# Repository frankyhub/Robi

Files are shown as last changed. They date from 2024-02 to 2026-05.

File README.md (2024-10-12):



<div align="center">

|[:skull:ISSUE](https://github.com/frankyhub/Robi/issues?q=is%3Aissue)|[:speech_balloon: Forum /Discussion](https://github.com/frankyhub/Robi/discussions)|[:grey_question:WiKi](https://github.com/frankyhub/Robi/wiki)||
|--|--|--|--|
| | | | |
||<a href="https://github.com/frankyhub/Robi/issues">|<a href="https://github.com/frankyhub/Robi/discussions">|<a href="https://github.com/frankyhub/Robi/releases">|
|| <a href="https://github.com/frankyhub/Robi/pulse" alt="Activity">| <a href="https://github.com/frankyhub/Robi/graphs/traffic">  |<a href="https://github.com/frankyhub?tab=stars"> |
</div>

# Robi
 ## 3D-Druck- und Lasercutter-Version

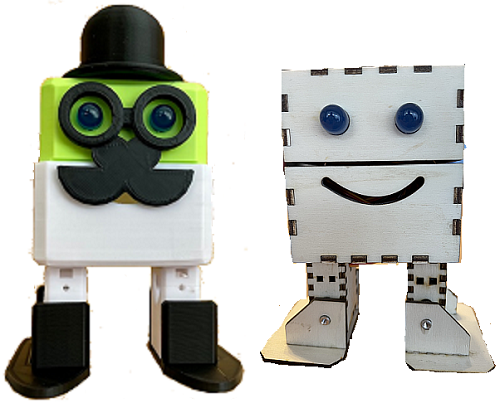
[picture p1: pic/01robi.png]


## Robi Lasercutter Montage Anleitung

## Story:
Diese Anleitung beschreibt die Montage eines Roboters. Robi kann laufen, tanzen und den Moonwalk. Jedes Bein hat zwei Gelenke, die von Servo-Motoren bewegt werden. Als Steuerung dient ein Arduino NANO, gespeist von einer 9V-Batterie.
Die Robi-Elemente werden aus einer 3mm Sperrholzplatte gelasert, ebenso ist ein 3D-Druck Gehäuse möglich.

## Entwerfe dein eigenes Robi Design mit Inkscape

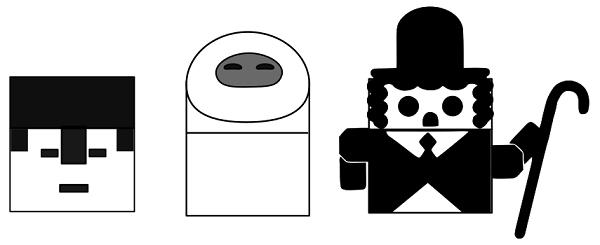
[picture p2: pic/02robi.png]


Downlaod [Inkscape-Vorlage](svg/Charley.svg)

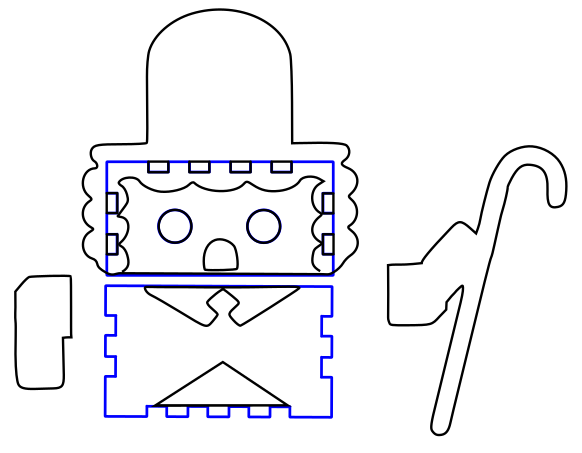
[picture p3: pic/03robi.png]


## Die Stückliste:

| Anzahl | Bezeichnung | 
| --- | --- |
| 1  | Sperrholzplatte 300x300x3mm  | 
|  1 | NANO-Shield  | 
| 1  | Arduino NANO V3  | 
|  1 | NANO-Shield  | 
| 1  |  40 Pin Male 2,54mm Stiftleisten einreihig für das NANO-Shield | 
|  1 |  40 Pin Female 2,54 mm Buchsenleiste einreihig für das NANO-Shield | 
| 1  | Schalter 1 polig  | 
| 2  | Jumbo LEDs  | 
| 1  | 1K Ohm Widerstand  | 
| 1  | 9V Batterie  | 
| 1  | 9V Batterie-Klipp  | 
| 4  | Servo Motore SG90  | 
| 2  | Zylinderkopf Schrauben M3x8  | 
| 1  | Kabelbinder 10cm  | 
| 1  | Holzleim  | 
| 1  | Sekundenkleber  | 
| 1  | 20cm Schaltlitze 0,25mm2  | 

## Bauteilbilder der Stückliste

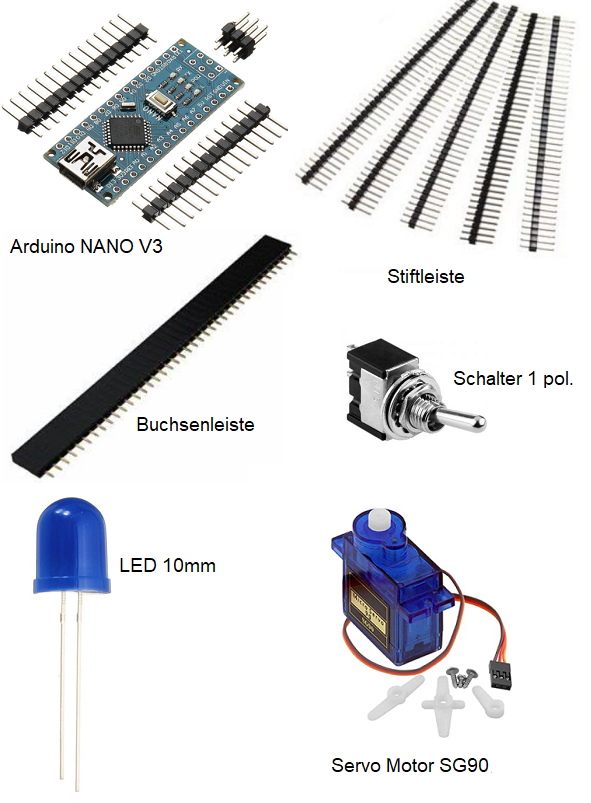
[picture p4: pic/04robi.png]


## Der NANO mit [Shield](https://github.com/frankyhub/KiCad-Shield/tree/main/NANO_Bot) und Stiftleisten

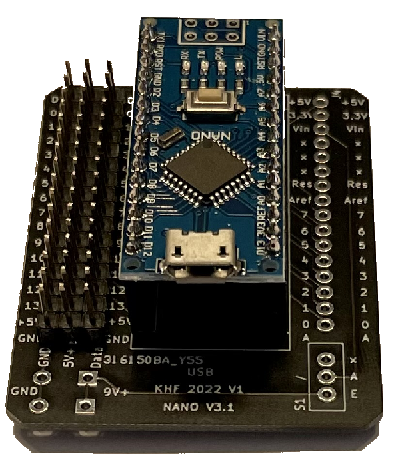
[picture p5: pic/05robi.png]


## Aufbau und Montage

Der Aufbau und die Montage von Robi ist in mehrere Schritte unterteilt

## Schritt 1: 
Überprüfe die Laserteile auf Vollständigkeit.
Verwende die Lasercutter Vorlage, bestehend aus:
+ 1 x Kopf Oberteilteil
+ 1 x Kopf Unterteil
+ 2 x Füße
+ 2 x Schuhe

Lasercutter-Datei (3mm Sperrholz)

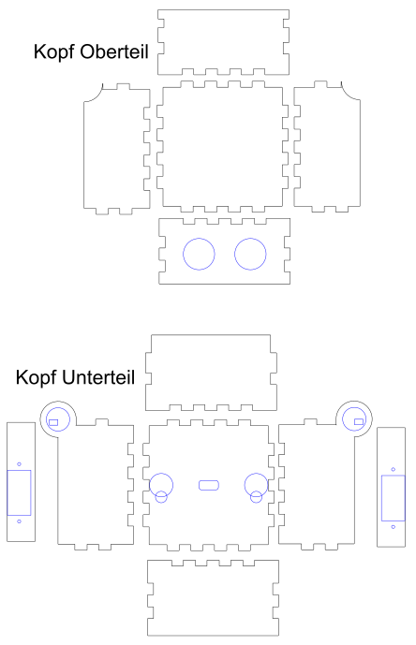
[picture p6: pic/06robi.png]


 Füße und Schuhe (3mm Sperrholz)

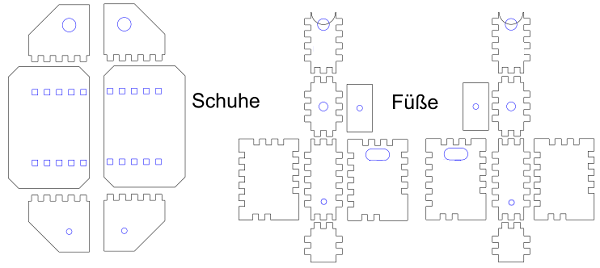
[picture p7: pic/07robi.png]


## Schritt 2: 
Das Kopf Oberteil montieren.

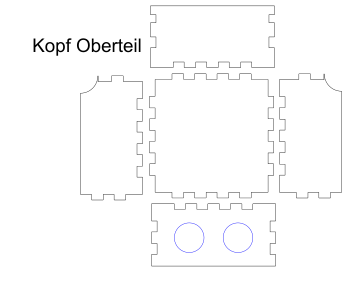
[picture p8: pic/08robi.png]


## Schritt 3: 
Das Kopf Unterteil montieren.
Achtung: Das rechte und linke Seitenteil mit dem Gelenk zum Schluss zusammen mit dem Kopf Oberteil montieren!

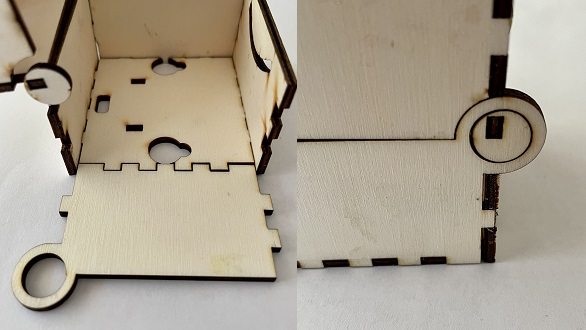
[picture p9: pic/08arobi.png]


Im Kopf Unterteil die Halterungen für die Servos kleben

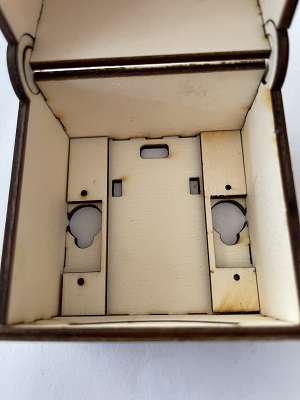
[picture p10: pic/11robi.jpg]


Die Hülle der beiden Füße verkleben.
Achtung: Wir benötigen zwei Füße. Die Öffnungen für die Servokabel sind jeweils innen und die Servos zeigen nach vorne!

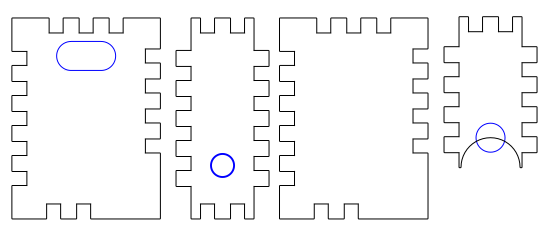
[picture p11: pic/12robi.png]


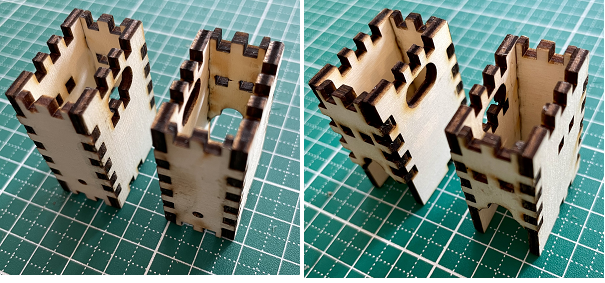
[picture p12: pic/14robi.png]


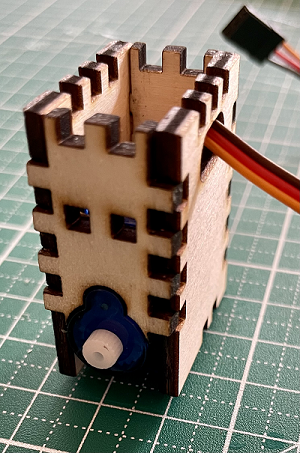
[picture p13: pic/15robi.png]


Die beiden Oberteile der Füße deckungsgleich verkleben (noch nicht an die Füße kleben!).

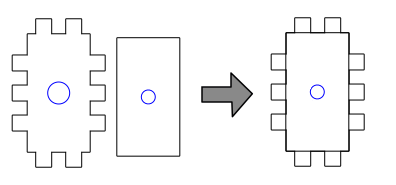
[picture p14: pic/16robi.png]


Die Oberteile der Füße werden an den Servo im Kopfteil geschraubt.

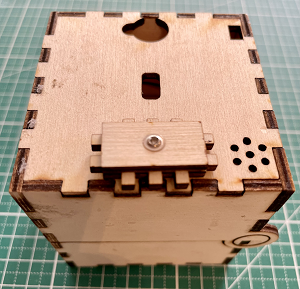
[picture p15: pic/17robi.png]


Alternativ können zu besseren Stabilität auch die 3D-Druck Teile verwendet werden.

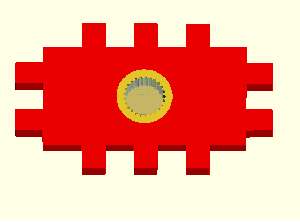
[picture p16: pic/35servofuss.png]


## Schritt 4: 
Den Robi verdrahten, die Bauteile jedoch noch nicht in das Gehäuse montieren.

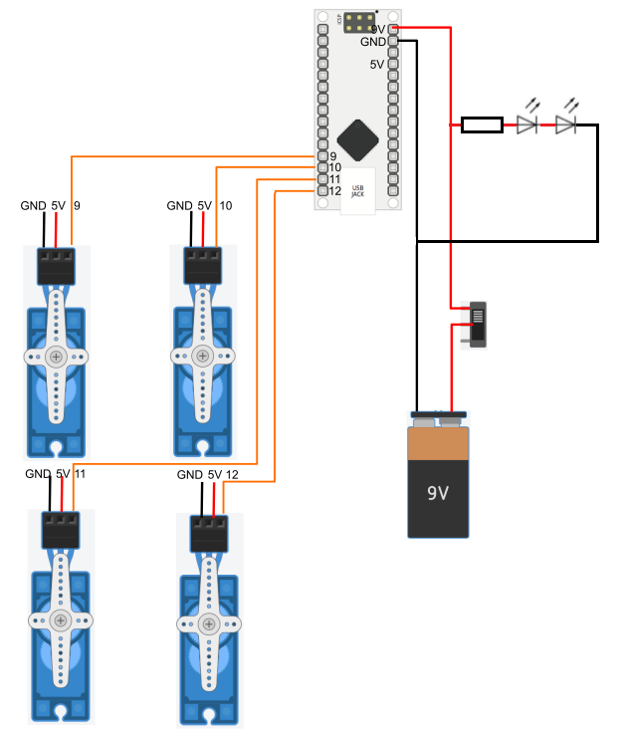
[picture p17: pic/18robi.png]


## Schritt 5: 
Vor der Montage der Servos ist ein Funktionstest sinnvoll:
Den Robi mit der Arduino IDE in C++ oder in Blocksprache programmieren.
Ist der Robi programmiert und sind die Servos in 90° Stellung, können sie in das Kopf-Unterteil und in die Füße montiert werden.

## Schritt 6: 
Die beiden Servos in 90° Stellung mit den unteren Kopfteil und den Oberteil der Füße verschrauben. Die Servos sollten durch die Verschraubung fest am Kopfteil sitzen. Anschließend die 9V-Batterie mit den Kabelbinder befestigen.

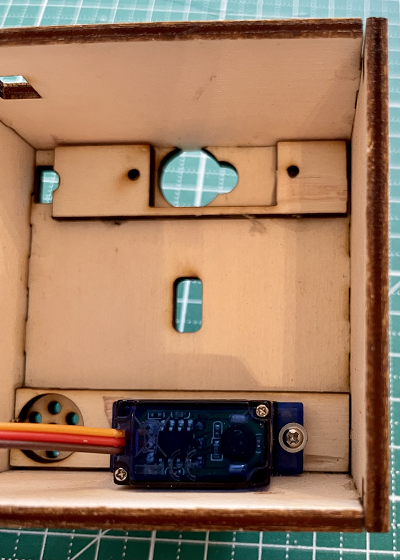
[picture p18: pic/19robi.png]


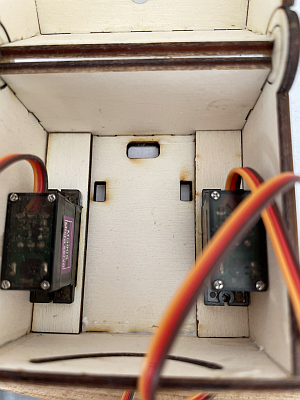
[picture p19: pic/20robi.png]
 

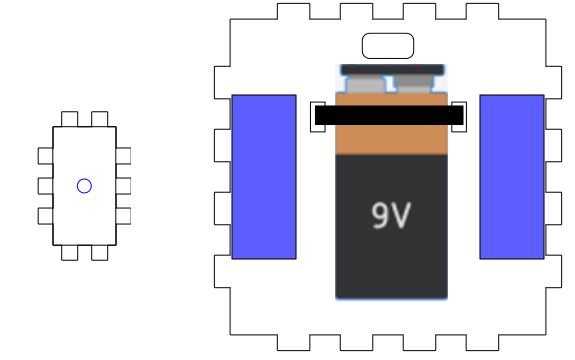
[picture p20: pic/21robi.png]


Die Schrittmotore in die Fußhülle montieren und das Fuß Unterteil ankleben

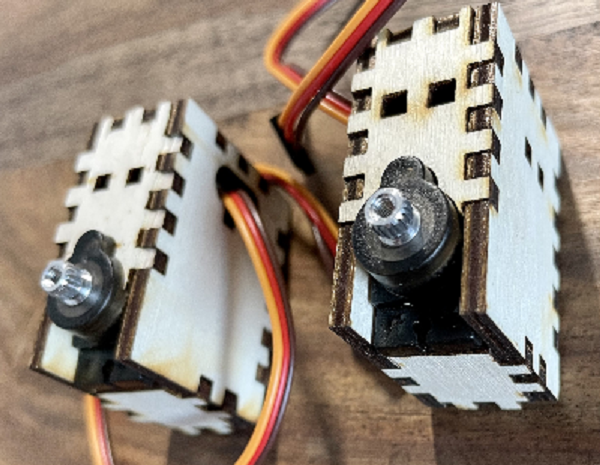
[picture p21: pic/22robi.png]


Die Schuhe an die Füße montieren

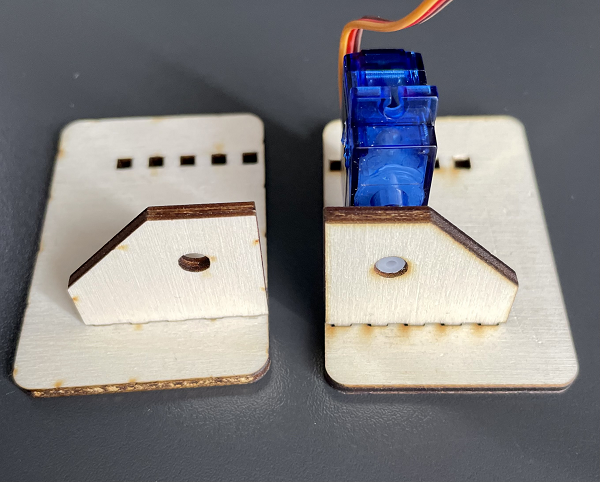
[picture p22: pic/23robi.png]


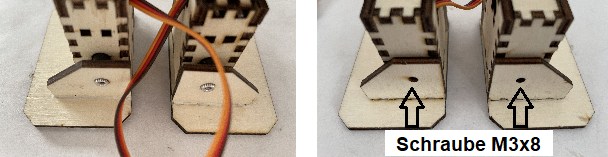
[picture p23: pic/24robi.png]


Die Servo-Kabel in den Body führen und die Füße an die Fußoberteile kleben

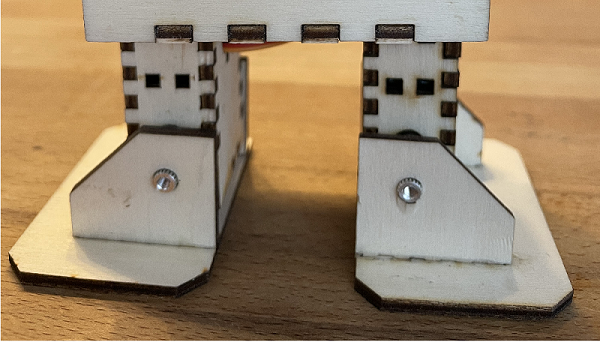
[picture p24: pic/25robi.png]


Alternativ können zu besseren Stabilität auch die 3D-Druck Teile verwendet werden.

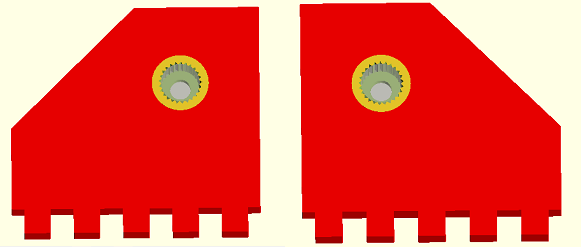
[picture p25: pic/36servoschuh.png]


## Schritt 7: 
Den NANO in das obere Kopfteil montieren
Platinenhalter auf das Shield kleben und das Shield anschließend in das innere, obere Kopfteil kleben. Daneben den Schalter montieren und verdrahten.
Vor dem endgültigen verkleben des NANOs in das Obere Kopfteil, sollte er fertig programmiert sein.
Optional noch zwei LEDs mit 1kOhm Vorwiderstand an 9V als Augen verwenden.

Einbau des NANO und der Battierie in den Robi-Kopfteil

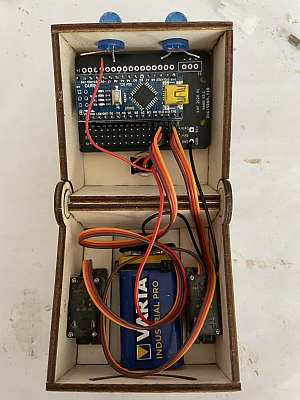
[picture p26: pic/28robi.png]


Anschlüsse der LEDs

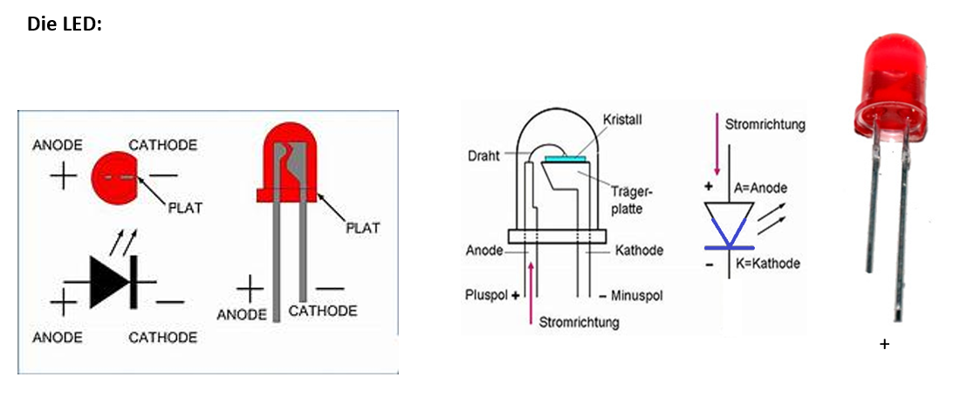
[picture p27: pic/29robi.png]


Anschluss des Batterieclips, des Schalters und der LEDs

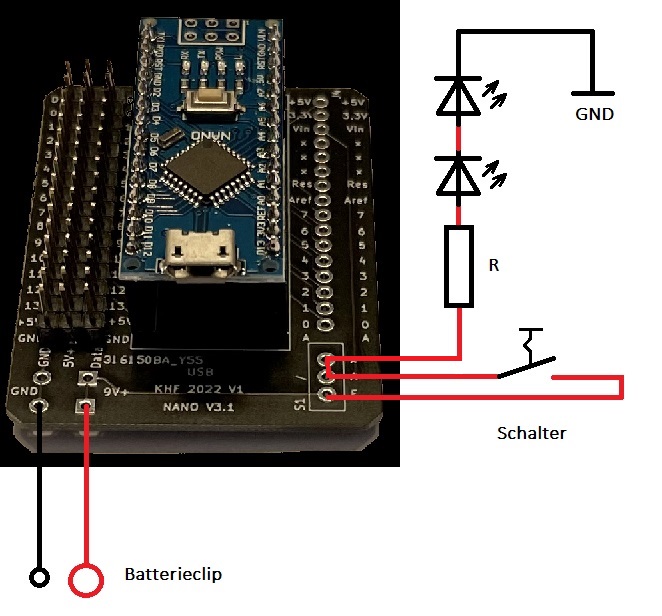
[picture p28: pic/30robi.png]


Fertig, Glückwunsch!

## Technische Hinweise

Anschlüsse des Servo-Motor SG90/MG90:

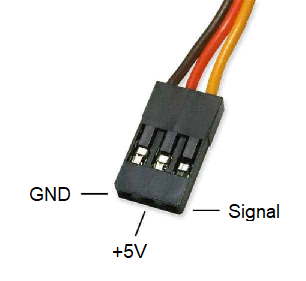
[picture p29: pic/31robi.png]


## Servo-Motor Impulsdiagramme:

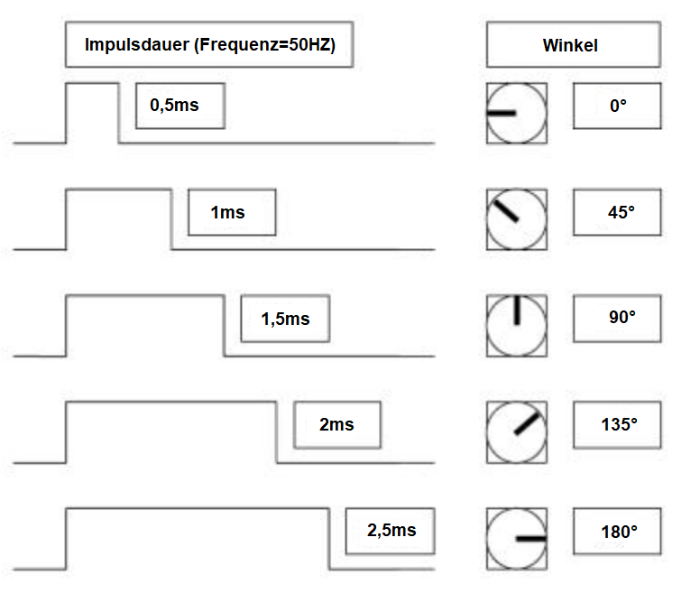
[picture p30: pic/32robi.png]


Impulsdiagramm: Ansteuerung des Servos mit einer Frequenz von 50 Hz:

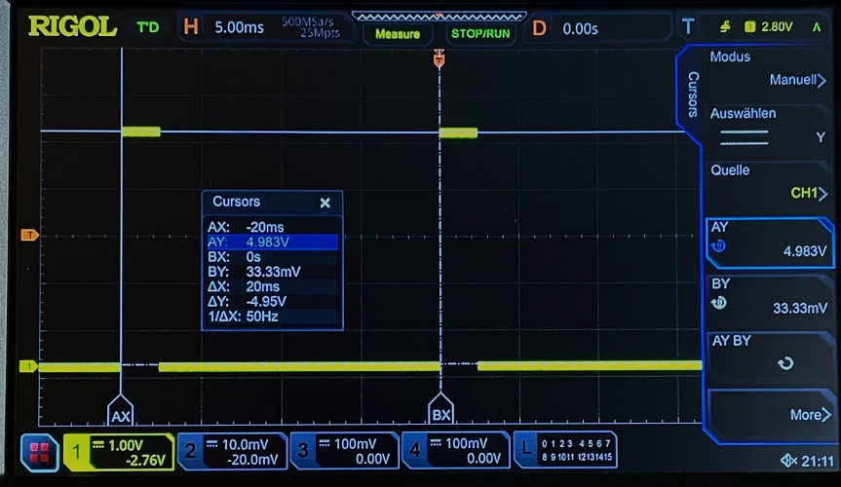
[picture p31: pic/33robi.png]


Impulsdiagramm: Ansteuerung des Servos mit einer Impulsbreite von 2,5ms (180°):

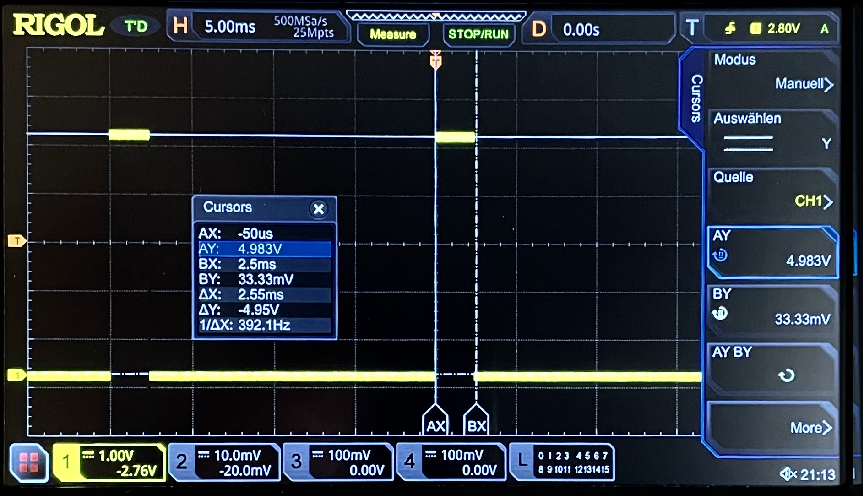
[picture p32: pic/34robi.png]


Blocky Beispiel Programme:

[Robi kalibirieren](blocky/robi_kalibrieren.bloc)

[Robi geht vorwärts](blocky/robi_vorwaerts.bloc)

[Robi tanzt I](blocky/robi_tanzt.bloc)

[Robi tanzt II](blocky/robi_zufall.bloc)

## Fertig!

---

<div style="position:absolute; left:2cm; ">   
<ol class="breadcrumb" style="border-top: 2px solid black;border-bottom:2px solid black; height: 45px; width: 900px;"> <p align="center"><a href="#oben">nach oben</a></p></ol>
</div>  

---

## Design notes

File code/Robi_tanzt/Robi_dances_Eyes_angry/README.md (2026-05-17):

## Robi angry eyes

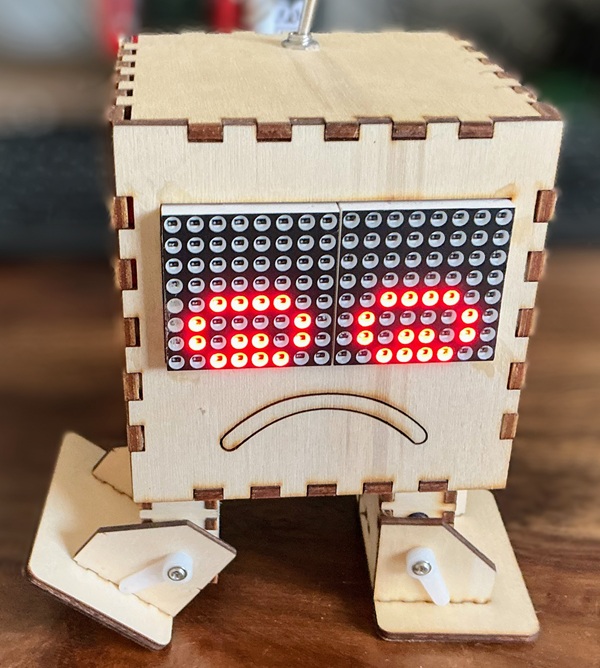
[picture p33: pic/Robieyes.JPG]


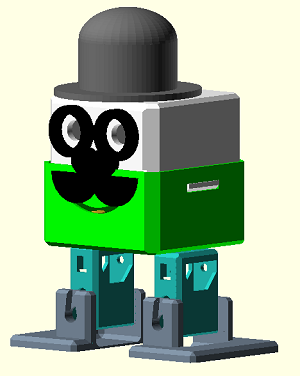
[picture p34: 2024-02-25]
pic/00robi.png

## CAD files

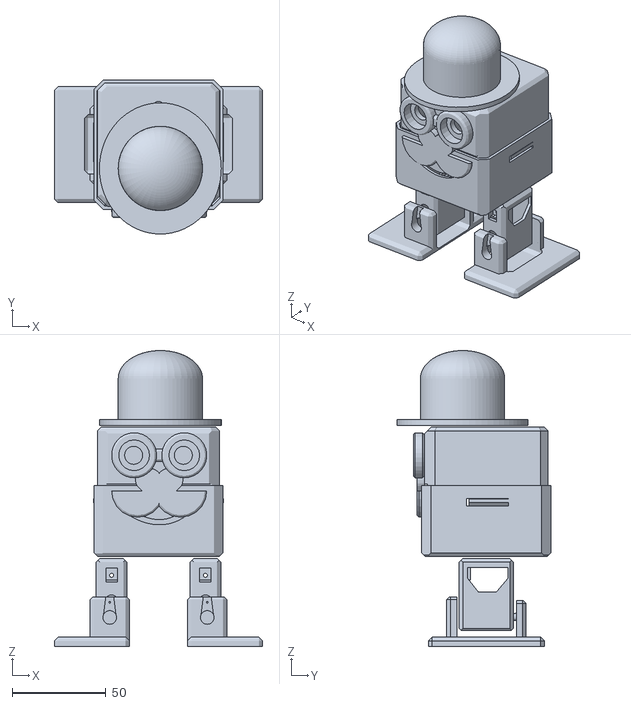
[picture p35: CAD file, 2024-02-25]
3D/Robi.stl
111.0 x 82.2 x 157.9

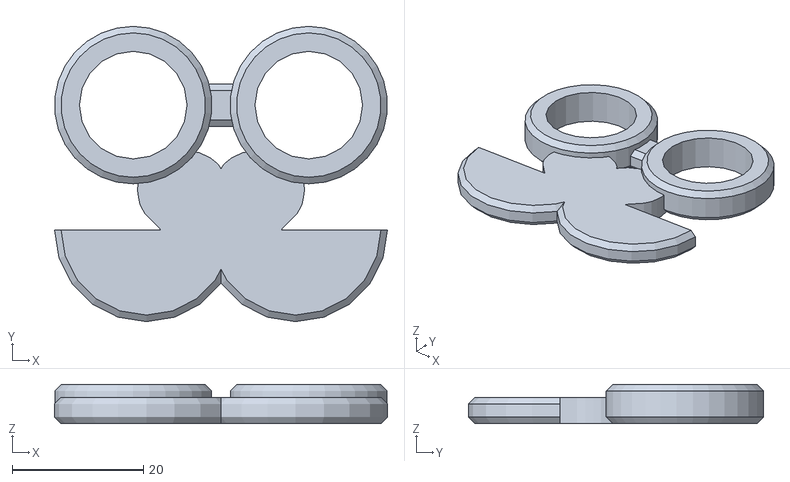
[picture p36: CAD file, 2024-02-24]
3D/Robi_Brille.stl
50.7 x 45.0 x 6.00

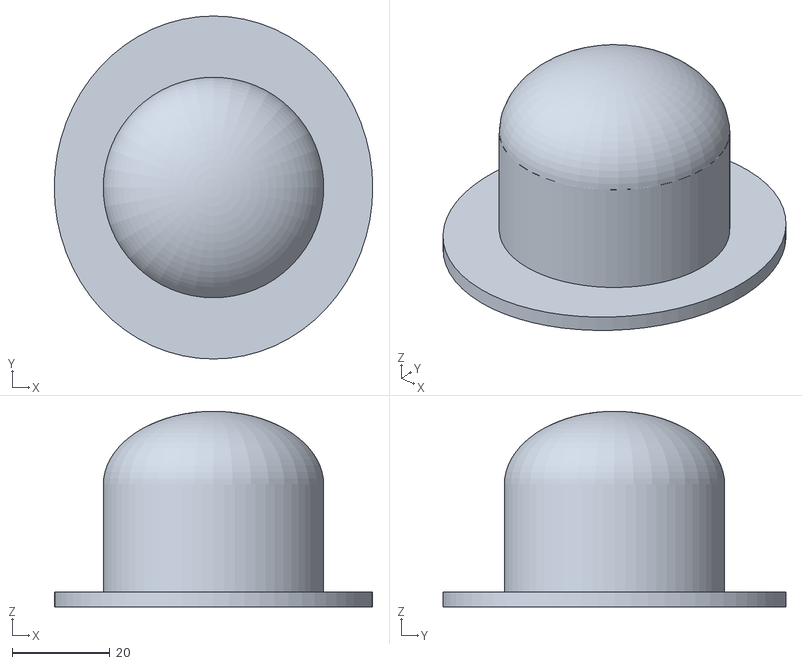
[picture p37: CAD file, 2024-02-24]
3D/Robi_Hut.stl
65.0 x 70.0 x 39.9

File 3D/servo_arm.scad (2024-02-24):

//Par. Servo Arm

arm_length = 7;

arm_count = 3; // [1,2,3,4,5,6,7,8]

//  Clear between arm head and servo head (PLA: 0.3, ABS 0.2)
SERVO_HEAD_CLEAR = 0.3; // [0.2,0.3,0.4,0.5]

$fn = 100 / 1;

/**
 *  Head / Tooth parameters
 *  Futaba 3F Standard Spline
 *  http://www.servocity.com/html/futaba_servo_splines.html
 *
 *  First array (head related) :
 *  0. Head external diameter
 *  1. Head heigth
 *  2. Head thickness
 *  3. Head screw diameter
 *
 *  Second array (tooth related) :
 *  0. Tooth count
 *  1. Tooth height
 *  2. Tooth length
 *  3. Tooth width
 */
FUTABA_3F_SPLINE = [
    [4.5, 5, 1.1, 2.5],
    [25, 0.4, 0.6, 0.0]
];

module servo_futaba_3f(length, count) {
    servo_arm(FUTABA_3F_SPLINE, [length, count]);
}

/**
 *  If you want to support a new servo, juste add a new spline definition array
 *  and a module named like servo_XXX_YYY where XXX is servo brand and YYY is the
 *  connection type (3f) or the servo type (s3003)
 */

module servo_standard(length, count) {
    servo_futaba_3f(length, count);
}

/**
 *  Tooth
 *
 *    |<-w->|
 *    |_____|___
 *    /     \  ^h
 *  _/       \_v
 *   |<--l-->|
 *
 *  - tooth length (l)
 *  - tooth width (w)
 *  - tooth height (h)
 *  - height
 *
 */
module servo_head_tooth(length, width, height, head_height) {
    linear_extrude(height = head_height) {
        polygon([[-length / 2, 0], [-width / 2, height], [width / 2, height], [length / 2,0]]);
    }
}

/**
 *  Servo head
 */
module servo_head(params, clear = SERVO_HEAD_CLEAR) {

    head = params[0];
    tooth = params[1];

    head_diameter = head[0];
    head_heigth = head[1];

    tooth_count = tooth[0];
    tooth_height = tooth[1];
    tooth_length = tooth[2];
    tooth_width = tooth[3];

    % cylinder(r = head_diameter / 2, h = head_heigth + 1);

    cylinder(r = head_diameter / 2 - tooth_height + 0.03 + clear, h = head_heigth);

    for (i = [0 : tooth_count]) {
        rotate([0, 0, i * (360 / tooth_count)]) {
            translate([0, head_diameter / 2 - tooth_height + clear, 0]) {
                servo_head_tooth(tooth_length, tooth_width, tooth_height, head_heigth);
            }
        }
    }
}

/**
 *  Servo hold
 *  - Head / Tooth parameters
 *  - Arms params (length and count)
 */
module servo_arm(params, arms) {

    head = params[0];
    tooth = params[1];

    head_diameter = head[0];
    head_heigth = head[1];
    head_thickness = head[2];
    head_screw_diameter = head[3];

    tooth_length = tooth[2];
    tooth_width = tooth[3];

    arm_length = arms[0];
    arm_count = arms[1];

    /**
     *  Servo arm
     *  - length is from center to last hole
     */
    module arm(tooth_length, tooth_width, head_height, head_heigth, hole_count = 1) {

        arm_screw_diameter = 2;

        difference() {
            union() {
                cylinder(r = tooth_width / 2, h = head_heigth);

                linear_extrude(height = head_heigth) {
                    polygon([
                        [-tooth_width / 2, 0], [-tooth_width / 3, tooth_length],
                        [tooth_width / 3, tooth_length], [tooth_width / 2, 0]
                    ]);
                }

                translate([0, tooth_length, 0]) {
                    cylinder(r = tooth_width / 3, h = head_heigth);
                }

                if (tooth_length >= 12) {
                    translate([-head_heigth / 2 + 2, 3.8, -4]) {
                        rotate([90, 0, 0]) {
                            rotate([0, -90, 0]) {
                                linear_extrude(height = head_heigth) {
                                    polygon([
                                        [-tooth_length / 1.7, 4], [0, 4], [0, - head_height + 5],
                                        [-2, - head_height + 5]
                                    ]);
                                }
                            }
                        }
                    }
                }
            }

            // Hole
            for (i = [0 : hole_count - 1]) {
                //translate([0, length - (length / hole_count * i), -1]) {
                translate([0, tooth_length - (4 * i), -1]) {
                    cylinder(r = arm_screw_diameter / 2, h = 10); //2 Loch 50 geschlossen
                }
            }

            cylinder(r = head_screw_diameter / 2, h = 10);
        }
    }

    difference() {
        translate([0, 0, 0.1]) {
            cylinder(r = head_diameter / 2 + head_thickness, h = head_heigth + 1);
        }

        cylinder(r = head_screw_diameter / 2, h = 10);

        servo_head(params);
    }

    arm_thickness = head_thickness;

    // Arm
    translate([0, 0, head_heigth]) {
        for (i = [0 : arm_count - 1]) {
            rotate([0, 0, i * (360 / arm_count)]) {
                arm(arm_length, head_diameter + arm_thickness * 2, head_heigth, 2);
            }
        }
    }
}

module demo() {
    rotate([0, 180, 0])
        servo_standard(arm_length, arm_count);
}

demo();

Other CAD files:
3D/servo_Fuss.scad
3D/servo_Schuh_Li.scad
3D/servo_Schuh_Re.scad
3D/Robi.scad

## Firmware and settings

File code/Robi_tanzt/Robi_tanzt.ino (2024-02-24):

/************************************************************************************************* 
                                      PROGRAMMINFO
************************************************************************************************** 
Funktion: ROBI tanzt 
**************************************************************************************************
Version: 03.09.2022
**************************************************************************************************
Board: NANO V3
**************************************************************************************************
C++ Arduino IDE V1.8.13
**************************************************************************************************
Einstellungen:
https://dl.espressif.com/dl/package_esp32_index.json
http://dan.drown.org/stm32duino/package_STM32duino_index.json
https://raw.githubusercontent.com/espressif/arduino-esp32/gh-pages/package_esp32_dev_index.json
************************************************************************************************* 
/*  03.09.2022
    RU.attach(12);    // Servo rechts oben an pin 8
    RL.attach(9);     // Servo rechts unten an pin 11 
    LU.attach(10);    // Servo links oben an pin pin 10 
    LL.attach(11);    // Servo links unten an pin 9 
*/
**************************************************************************************************/


#include "VarSpeedServo.h"  
#include <NewPing.h>        
//#include <Servo.h>
/*  03.09.2022
    RU.attach(12);    // Servo rechts oben an pin 12
    RL.attach(9);     // Servo rechts unten an pin 9 
    LU.attach(10);    // Servo links oben an pin pin 10 
    LL.attach(11);    // Servo links unten an pin 11 
*/    

VarSpeedServo RU;  
VarSpeedServo RL;  
VarSpeedServo LU;  
VarSpeedServo LL;  

NewPing sonar(4,3,200); 
                                                     //vel(min), delay_Forward(max) = (5, 2000) 
const int vel = 40, vel_Back = 15;                   //vel(mid), delay_Forward(mid) = (20, 750) 
const int delay_Forward = 300, delay_Back = 750;     //vel(max), delay_Forward(min)= (256, 50)
                                                     //Empfelung ---> (10, 700) (50, 500) (100, 100) (100, 300) (100, 500)

int vel_Dance1 = 30,    vel_Dance2 = 25,    vel_Dance3 = 40;     
int delay_Dance1 = 300, delay_Dance2 = 750, delay_Dance3 = 200;  

int vel_Dance4 = 40,    vel_Dance5 = 40,    vel_Dance6 = 30;
int delay_Dance4 = 400, delay_Dance5 = 400, delay_Dance6 = 500;

const int array_cal[4] = {90,90,90,90};    
int RU_Degree = 0, LU_Degree = array_cal[2] + 5;

const int num_dance1 = 10;
const int array_dance1[num_dance1][4] =
{ 
//slide links 0-4
    {0,-20,0,0},  
    {0,-40,0,20},
    {0,-20,0,40},
    {0,0,0,20},
    {0,0,0,0},
    
//slide rechts 5-9
    {0,0,0,20},  
    {0,-20,0,40},
    {0,-40,0,20},
    {0,-20,0,0},
    {0,0,0,0}, 
};

const int num_dance2 = 32;
const int array_dance2[num_dance2][4] =
{ 
//linker Fuß 0-15
    {20,0,40,0},
    {20,-30,40,-30}, 
    {20,-30,10,-30},
    {20,-30,40,-30}, 
    {20,-30,10,-30},

    {20,-30,40,-30}, 
    {20,0,40,-30},
    {20,80,40,-30},
    {20,0,40,-30},
    {20,-80,40,-30},        
    {20,0,40,-30},
    {20,80,40,-30},
    {20,0,40,-30},
    {20,-30,40,-30},    
    {20,0,40,0},
    {0,0,0,0}, 
     
//rechter Fuß 16-31
    {-40,0,-20,0},
    {-40,40,-20,30}, 
    {-20,40,-20,30}, 
    {-40,40,-20,30}, 
    {-20,40,-20,30}, 

    {-40,40,-20,30}, 
    {-40,40,-20,0},
    {-40,40,-20,-80},
    {-40,40,-20,0},
    {-40,40,-20,80},        
    {-40,40,-20,0},
    {-40,40,-20,-80},
    {-40,40,-20,0},
    {-40,40,-20,30},    
    {-40,0,-20,0},
    {0,0,0,0},
};

const int num_dance3 = 8;        //split step
const int array_dance3[num_dance3][4] =
{ 
    {0,-40,0,0},
    {20,-30,20,20},
    {40,0,40,30},   
    {0,0,0,40},
    {-20,-20,-20,30},
    {-40,-30,-40,0},

    {0,-40,0,0},
    {0,0,0,0},
};

const int num_dance4 = 20;      //nach innen und beschleunigen
const int array_dance4[num_dance4][4] =
{     
    {0,-20,0,20},   
    {0,0,0,0},
    {0,-20,0,20},
    {0,0,0,0},
    {0,-20,0,20},
    {0,0,0,0},
    {0,-20,0,20},
    {0,0,0,0},
    
    {0,-50,0,50},
    {0,0,0,0},    
    {0,-50,0,50},
    {0,0,0,0},    
    {0,-50,0,50},
    {0,0,0,0},    
    {0,-50,0,50},
    {0,0,0,0},
    
    {0,-40,0,40},
    {0,-50,0,50},
    {0,-60,0,60},
    {0,0,0,0,},
};

const int num_dance5 = 17;
const int array_dance5[num_dance5][4] =
{ 
    {35,0,15,0},    //beide Beine berühren lassen
    {35,30,15,30},   
    {-35,30,15,30},   
    {-20,0,15,0},
    {0,0,0,0},

    {0,-40,0,40},    //nach innen und drehen Beine
    {-30,-40,-20,40},
    {0,-40,0,40},
    {20,-40,30,40},    

    
    {0,-40,0,40},    //An Ort und Stelle auf und ab gehen und Beine drehen
    {20,-40,-20,40},   
    {20,-20,-20,20},
    {20,0,-20,0},   
    {-20,-10,20,10},
    {-10,-30,10,30},

    {0,-40,0,40},
    {0,0,0,0},
};

const int num_dance6 = 32;      
const int array_dance6[num_dance6][4] =
{   
    {0,-40,0,-20},        //weitergehen
    {25,-40,18,-20},
    {25,0,18,0},
    {0,20,0,40},
    {-18,20,-25,40},
    {-18,0,-25,0},
      
    {0,-40,0,-20},        //rausziehen
    {25,-40,18,-20},
    {0,0,0,0},
    {0,20,0,40},
    {-18,20,-25,40},
    {0,0,0,0},

    {0,-40,0,-20},        //rausziehne - zurück
    {-25,-40,-18,-20},
    {-25,0,-18,0},
    {0,20,0,40},
    {18,20,25,40},
    {18,0,25,0},

    {0,-40,0,-20},        //vorwärts
    {30,-40,30,-20},
    {30,0,30,0},
    {0,20,0,40},
    {-30,20,-30,40},
    {-30,0,-30,0},
  
    {0,-40,0,-20},        //zurück
    {-30,-40,-30,-20},
    {-30,0,-30,0},
    {0,20,0,40},
    {30,20,30,40},
    {30,0,30,0},

    {15,0,15,0},
    {0,0,0,0},
};

//Programmauswahl - Nur EIN Programm aktivieren!!!
//#define INSTALL
//#define CALIBRATION
#define RUN

void Servo_Init()
/*
    RU.attach(12);    // Servo rechts oben an pin 8
    RL.attach(9);   // Servo rechts unten an pin 11 
    LU.attach(10);   // Servo links oben an pin pin 10 
    LL.attach(11);   // Servo links unten an pin 9 
*/
{
    RU.attach(12);    // Servo rechts oben an pin 8
    RL.attach(9);   // Servo rechts unten an pin 11 
    LU.attach(10);   // Servo links oben an pin pin 10 
    LL.attach(11);   // Servo links unten an pin 9 

}

void Adjust()                            // Vermeide das schnelle Spinnen des Servos bei der Initialisierung
{                                        // RU,LU geht von array_cal[0] - 5 ,array_cal[2] + 5 Grad auf array_cal[0],array_cal[2] Grad
    for(RU_Degree = array_cal[0] - 5; RU_Degree <= array_cal[0]; RU_Degree += 1) {
        RU.write(RU_Degree);             // in Schritten von 1 Grad
        LU.write(LU_Degree--);           // sage den Servo, dass er zu RU_Degreeition gehen soll, LU_Degreeition in der Variable "RU_Degree", "LU_Degree"       
        delay(15);                       // wartet 15ms, bis der Servo die RU_Degreeition erreicht hat
    }
}

bool TooClose()
{
    int tooclose = 0;
    for(int a=0; a<5; a++) {  
        delay(50);
        int din = sonar.ping_in();
        if (din < 7 && din > 0) tooclose++;
    }
    if (tooclose < 5) return 1;   
    return 0;
}

void Slide_2_Left(int times)
{
    for(int time1 = 0; time1 < times; time1++) { 
        for(int z=0; z<5; z++) {                     
            RU.slowmove (array_cal[0] + array_dance1[z][0] , vel_Dance1);   
            RL.slowmove (array_cal[1] + array_dance1[z][1] , vel_Dance1);
            LU.slowmove (array_cal[2] + array_dance1[z][2] , vel_Dance1);
            LL.slowmove (array_cal[3] + array_dance1[z][3] , vel_Dance1);
            delay(delay_Dance1); 
        } 
    }
}

void Slide_2_Right(int times)
{
    for(int time1 = 0; time1 < times; time1++) {
        for(int z=5; z<10; z++) {                     
            RU.slowmove (array_cal[0] + array_dance1[z][0] , vel_Dance1);   
            RL.slowmove (array_cal[1] + array_dance1[z][1] , vel_Dance1);
            LU.slowmove (array_cal[2] + array_dance1[z][2] , vel_Dance1);
            LL.slowmove (array_cal[3] + array_dance1[z][3] , vel_Dance1);
            delay(delay_Dance1); 
        }   
    }
}

void Left_Foot_Support()
{
    for(int z=0; z<16; z++) { //z<12
        if ( z > 5 && z < 14) {   //z(1,10)
            vel_Dance2 = 50;
            delay_Dance2 = 200;
        }
        else { 
        vel_Dance2 = 25; 
        delay_Dance2 = 750;
        }
                    
        RU.slowmove (array_cal[0] + array_dance2[z][0] , vel_Dance2);   
        RL.slowmove (array_cal[1] + array_dance2[z][1] , vel_Dance2);
        LU.slowmove (array_cal[2] + array_dance2[z][2] , vel_Dance2);
        LL.slowmove (array_cal[3] + array_dance2[z][3] , vel_Dance2);
        delay(delay_Dance2); 
    }
}

void Right_Foot_Support()
{
    for(int z=16; z<32; z++) { //z<24
        if ( z > 21 && z < 30) {   //z(13,22)
            vel_Dance2 = 50;
            delay_Dance2 = 200;
        }
        else { 
        vel_Dance2 = 25; 
        delay_Dance2 = 750;
        }
                    
        RU.slowmove (array_cal[0] + array_dance2[z][0] , vel_Dance2);   
        RL.slowmove (array_cal[1] + array_dance2[z][1] , vel_Dance2);
        LU.slowmove (array_cal[2] + array_dance2[z][2] , vel_Dance2);
        LL.slowmove (array_cal[3] + array_dance2[z][3] , vel_Dance2);
        delay(delay_Dance2); 
    }
}

void Dancing1_2()
{
    Slide_2_Left(2);
    Left_Foot_Support();
    
    Slide_2_Right(2);
    Right_Foot_Support();
}

void Dancing3(int Times = 1, int Vel = 40, int Delay = 250, int low = 0, int high = 0)
{   
    for(int time3 = 0; time3 < Times; time3++) {
        for(int z=0; z<6; z++) {
            if ( time3 > 1 && time3 < 4) {
            vel_Dance3 = Vel;
            delay_Dance3 = Delay;
            }
            else { 
            vel_Dance3 = 40; 
            delay_Dance3 = 200;
            }                     
            
            RU.slowmove (array_cal[0] + array_dance3[z][0] , vel_Dance3);   
            RL.slowmove (array_cal[1] + array_dance3[z][1] , vel_Dance3);
            LU.slowmove (array_cal[2] + array_dance3[z][2] , vel_Dance3);
            LL.slowmove (array_cal[3] + array_dance3[z][3] , vel_Dance3);
            delay(delay_Dance3); 
        } 
    }
    for(int z=6; z<8; z++) {                     
            RU.slowmove (array_cal[0] + array_dance3[z][0] , vel_Dance3);   
            RL.slowmove (array_cal[1] + array_dance3[z][1] , vel_Dance3);
            LU.slowmove (array_cal[2] + array_dance3[z][2] , vel_Dance3);
            LL.slowmove (array_cal[3] + array_dance3[z][3] , vel_Dance3);
            delay(delay_Dance3); 
        }       
}

void Dancing4()
{  
    for(int z=0; z<num_dance4; z++) {
        if ( z > 17) {
            vel_Dance4 = 10;
            delay_Dance4 = 1500;
            }
        else {
            vel_Dance4 = 40;
            delay_Dance4 = 400;
            }
                 
        RU.slowmove (array_cal[0] + array_dance4[z][0] , vel_Dance4);   
        RL.slowmove (array_cal[1] + array_dance4[z][1] , vel_Dance4);
        LU.slowmove (array_cal[2] + array_dance4[z][2] , vel_Dance4);
        LL.slowmove (array_cal[3] + array_dance4[z][3] , vel_Dance4);
        delay(delay_Dance4); 
    } 
}

void Dancing5()
{   
    for(int x = 0; x < 3; x++) {
        for(int z=0; z<5; z++) {                     
            RU.slowmove (array_cal[0] + array_dance5[z][0] , vel_Dance5);   
            RL.slowmove (array_cal[1] + array_dance5[z][1] , vel_Dance5);
            LU.slowmove (array_cal[2] + array_dance5[z][2] , vel_Dance5);
            LL.slowmove (array_cal[3] + array_dance5[z][3] , vel_Dance5);
            delay(delay_Dance5); 
        } 
    }
   
    for(int x = 0; x < 2; x++) {
        for(int z=5; z<9; z++) {                     
            RU.slowmove (array_cal[0] + array_dance5[z][0] , 30);   
            RL.slowmove (array_cal[1] + array_dance5[z][1] , 30);
            LU.slowmove (array_cal[2] + array_dance5[z][2] , 30);
            LL.slowmove (array_cal[3] + array_dance5[z][3] , 30);
            delay(550); 
        } 
    }
    
    for(int x = 0; x < 3; x++) {
        for(int z=9; z<15; z++) {                     
            RU.slowmove (array_cal[0] + array_dance5[z][0] , vel_Dance5);   
            RL.slowmove (array_cal[1] + array_dance5[z][1] , vel_Dance5);
            LU.slowmove (array_cal[2] + array_dance5[z][2] , vel_Dance5);
            LL.slowmove (array_cal[3] + array_dance5[z][3] , vel_Dance5);
            delay(300); 
        } 
    }    
    for(int z=15; z<17; z++) {                     
            RU.slowmove (array_cal[0] + array_dance5[z][0] , 10);   
            RL.slowmove (array_cal[1] + array_dance5[z][1] , 10);
            LU.slowmove (array_cal[2] + array_dance5[z][2] , 10);
            LL.slowmove (array_cal[3] + array_dance5[z][3] , 10);
            delay(1500); 
        }   
}

void Dancing6()
{   
    const int array_cal_0 = array_cal[0] + 10 , array_cal_2 = array_cal[2] - 10;
    
    for(int x = 0; x < 3; x++) {
        for(int z=0; z<6; z++) {                     
            RU.slowmove (array_cal_0 + array_dance6[z][0] , vel_Dance6);   
            RL.slowmove (array_cal[1] + array_dance6[z][1] , vel_Dance6);
            LU.slowmove (array_cal_2 + array_dance6[z][2] , vel_Dance6);
            LL.slowmove (array_cal[3] + array_dance6[z][3] , vel_Dance6);
            delay(delay_Dance6); 
        } 
    }
   
    for(int x = 0; x < 3; x++) {
        for(int z=6; z<12; z++) {                     
            RU.slowmove (array_cal_0 + array_dance6[z][0] , 40);   
            RL.slowmove (array_cal[1] + array_dance6[z][1] , 40);
            LU.slowmove (array_cal_2 + array_dance6[z][2] , 40);
            LL.slowmove (array_cal[3] + array_dance6[z][3] , 40);
            delay(400); 
        } 
    }
    
    for(int x = 0; x < 3; x++) {
        for(int z=12; z<18; z++) {                     
            RU.slowmove (array_cal_0 + array_dance6[z][0] , vel_Dance6);   
            RL.slowmove (array_cal[1] + array_dance6[z][1] , vel_Dance6);
            LU.slowmove (array_cal_2 + array_dance6[z][2] , vel_Dance6);
            LL.slowmove (array_cal[3] + array_dance6[z][3] , vel_Dance6);
            delay(delay_Dance6); 
        } 
    }  
    for(int x = 0; x < 3; x++) {
        for(int z=18; z<24; z++) {                     
            RU.slowmove (array_cal[0] + array_dance6[z][0] , vel_Dance6);   
            RL.slowmove (array_cal[1] + array_dance6[z][1] , vel_Dance6);
            LU.slowmove (array_cal[2] + array_dance6[z][2] , vel_Dance6);
            LL.slowmove (array_cal[3] + array_dance6[z][3] , vel_Dance6);
            delay(delay_Dance6); 
        } 
    }

    for(int x = 0; x < 3; x++) {
        for(int z=24; z<30; z++) {                     
            RU.slowmove (array_cal[0] + array_dance6[z][0] , vel_Dance6);   
            RL.slowmove (array_cal[1] + array_dance6[z][1] , vel_Dance6);
            LU.slowmove (array_cal[2] + array_dance6[z][2] , vel_Dance6);
            LL.slowmove (array_cal[3] + array_dance6[z][3] , vel_Dance6);
            delay(delay_Dance6); 
        } 
    }
    for(int z=30; z<32; z++) {                     
            RU.slowmove (array_cal[0] + array_dance5[z][0] , 10);   
            RL.slowmove (array_cal[1] + array_dance5[z][1] , 10);
            LU.slowmove (array_cal[2] + array_dance5[z][2] , 10);
            LL.slowmove (array_cal[3] + array_dance5[z][3] , 10);
            delay(1500); 
        }     
}
    
void setup()  
{
#ifdef INSTALL
    Servo_Init();
  
    RU.slowmove (90 , vel);
    RL.slowmove (90 , vel);
    LU.slowmove (90 , vel);
    LL.slowmove (90 , vel);
    while(1);
#endif

#ifdef CALIBRATION 
    Servo_Init();  
    Adjust();
    
    RL.slowmove (array_cal[1] , vel);
    LL.slowmove (array_cal[3] , vel);
    delay(2000);
    while(1);
#endif

#ifdef RUN 
    Servo_Init();
    Adjust(); 
       
    RL.slowmove (array_cal[1] , vel);
    LL.slowmove (array_cal[3] , vel);
    delay(2000);
#endif
}

void loop() 
{   
    Dancing1_2();
    delay(500);    
    Dancing3(5,20,400);
    delay(500);    
    Dancing4();
    delay(500);    
    Dancing5();
    delay(500);    
    Dancing6();
    delay(500); 
    while(1);
     
}

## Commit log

2024-02-24 V1.0 24.02.2024
    [OttoDIY_mustache.stl, Otto_Chaplin_Hat.stl, Robi.scad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]
2024-02-25 V1.2 25.02.2024
    [servo_Schuh_Li.scad]
2024-02-25 V1.3 25.02.2024
    [Robi.scad, Robi.stl]
